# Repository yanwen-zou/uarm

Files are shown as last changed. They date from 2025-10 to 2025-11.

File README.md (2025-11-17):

# 🤖 Lerobot Anything








<p align="center">
  xArm Demo
  Dobot Demo
  ARX Demo
</p>

---

> **🚀 Bringing Leader-Follower teleoperation system to every real robot and robot arm -- Cheaper, Smoother, Plug-and-Play**
> **💵 Starts from $60 cost!! Then controls any robot arm system!!**

*Built upon the giants: [LeRobot](https://github.com/huggingface/lerobot), [SO-100/SO-101](https://github.com/TheRobotStudio/SO-ARM100), [XLeRobot](https://github.com/Vector-Wangel/XLeRobot#), [Gello](https://github.com/wuphilipp/gello_mechanical/tree/main)*

# 📰 News
- 2025-11-10: **Global version** based on Feetech STS3215 servo is launched! Chech [here](https://docs.google.com/document/d/1dUN4sJhYx_iuS_rFvj-YpyX4Y7nneRDTKJxCQ7PTXpY/edit?usp=sharing).
- 2025-11-1: We add support for SO-100 and XLeRobot Teleoperation! Check [here](github.com/MINT-SJTU/LeRobot-Anything-U-Arm/tree/main/src/uarm/scripts/Follower_Arm/LeRobot).
- 2025-09-10: STEP files of 3 configs are uploaded.
- 2025-09-08: Hardware Assembly Video Uploaded! We also open-sourced 5 datasets collected by UArm with XArm6 at [our huggingface page](https://huggingface.co/MINT-SJTU)
- 2025-08-15: **LeRobot Anything UArm 0.1.0** hardware setup, the 1st version fully capable for three major robot arm configurations, starts from 60$.

---

# 📋 Table of Contents

- [Overview](#-overview)
- [✨ Features](#-features)
- [💵 Total Cost](#-total-cost-)
- [🤖 Supported Robots (find your robot in the list!)](#-supported-robots)
- [🚀 Quick Start](#-quick-start)
- [🔮 Roadmap](#-roadmap)
- [🤝 Contributing](#-contributing)
- [🔧 Tired of DIY? Order Now](#-Order-Link)
---

## 🎯 Overview

LeRobot Anything is a **low-cost, universal, leader-follower teleoperation system** for any commercial robot arms through 3 hardware configurations. Designed for researchers, educators, and robotics enthusiasts, it provides a standardized interface for diverse robot platforms. This project focus on extending the Lerobot to control any real robot in both real scene and simulation. 

For detail, see our technical report [here](https://arxiv.org/abs/2509.02437).

### 🎯 Target Environment (Docker coming soon)

- **OS**: Ubuntu 20.04
- **ROS**: Noetic
- **Simulation**: SAPIEN integration (Built upon [ManiSkill](https://github.com/haosulab/ManiSkill))

---

## ✨ Features

| Feature | Description |
| --- | --- |
| 🔄**Universal Compatibility** | Four teleop configurations covering **most (95%) commercial robot arms** |
| 📡**ROS Integration** | Native ROS1 support with `/servo_angles` topic publishing |
| 🎮**Real-time Control** | Low-latency joint-space control |
| 🔌**Plug & Play** | Easy follower-arm integration with provided examples |
| 🛠️**Extensible** | Simple API for adding new robot support |
| 💰**Cost-effective** | Ultra low-cost hardware solution |
| 🎯**Optimized Hardware** | Move smoothly and flexibly |
| 💻**Simulation Test** | Support teleoperation test in simulation environment |

### 🎮 Ready-to-Use Examples

**Real Robot Examples:**

<p align="center">

| Dobot CR5 | xArm Series | ARX5 |
|---|---|---|
| Dobot CR5 Real Robot | xArm Series Real Robot | ARX5 Real Robot |

</p>

**Simulation Examples:**

<p align="center">

| SO100 | ARX-X5 | XLeRobot |
|---|---|---|
| SO100 Simulation | ARX-X5 Simulation | XLeRobot Simulation |

| xArm Series | Franka Panda | Piper |
|---|---|---|
| xArm Series Simulation | Franka Panda Simulation | Piper Simulation |

</p> 

## 💵 Total Cost 💵

> [!NOTE]
> Cost excludes 3D printing, tools, shipping, and taxes.

| Price | US | EU | CN |
| --- | --- | --- | --- |
| **Basic** (use your laptop) | **~$60** | **~€60** | **~¥360** |
| ↑ Servos | +$60 | +€60 | +¥405 |

---

## 🤖 Supported Robots (find your robot in the list!)

| Configuration | Compatible Robot Arms | Status |
| --- | --- | --- |
| [**Config 1**](https://github.com/MINT-SJTU/LeRobot-Anything-U-Arm/tree/main/mechanical/Config1_STL) | Xarm6, Fanuc LR Mate 200iD, Trossen ALOHA, Agile PiPER, Realman RM65B, KUKA LBR iiSY Cobot | ✅ Ready |
| [**Config 2**](https://github.com/MINT-SJTU/LeRobot-Anything-U-Arm/tree/main/mechanical/Config2_STL) | Dobot CR5, UR5, ARX R5*, AUBO i5, JAKA Zu7 | ✅ Ready |
| [**Config 3**](https://github.com/MINT-SJTU/LeRobot-Anything-U-Arm/tree/main/mechanical/Config3_STL) | Franka FR3, Franka Emika Panda, Flexiv Rizon, Realman RM75B , Xarm7 | ✅ Ready |

> 💡 **This is only part of our supported robots! For more robots, you can compare their mechanical configuration with each U-Arm to confirm which one fits your need (in most cases it will).

---

## 🚀 Quick Start

> [!NOTE]
> If you are totally new to programming, please spend at least a day to get yourself familiar with basic Python, Ubuntu and GitHub (with the help of Google and AI). At least you should know how to set up Ubuntu system, git clone, pip install, use interpreters (VS Code, Cursor, PyCharm, etc.) and directly run commands in the terminals.

1. 💵 **Buy your parts**: [Bill of Materials](https://docs.google.com/document/d/1TjhJOeJXsD5kmoYF-kuWfPju6WSUeSnivJiU7TH4vWs/edit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)
2. 🖨️ **Print your stuff**: [3D printing](https://github.com/MINT-SJTU/Lerobot-Anything-U-arm/tree/main/mechanical)
3. 🔨 **Assemble**! [Assembly Guide](https://www.youtube.com/watch?v=-gpYuN2LlVs)
4. 💻 **Software Env Set up & Real-world Teleop**: [Get your robot moving!](https://github.com/MINT-SJTU/Lerobot-Anything-Uarm/blob/main/howtoplay.md)
5. 🎮 **Simulation**: [Try it out in SAPIEN!](https://github.com/MINT-SJTU/Lerobot-Anything-U-arm/blob/main/src/simulation/README.md)

For detailed hardware guide, check  [Hardware Guide](https://docs.google.com/document/d/1TjhJOeJXsD5kmoYF-kuWfPju6WSUeSnivJiU7TH4vWs/edit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)

---

## 🔮 Roadmap

### 🎯 TO-DO List

- [X] **SAPIEN Simulation Environment**: Install and Play!

  - Virtual teleop setup mirroring physical hardware
  - Rapid prototyping and testing capabilities
  - Integration with existing SAPIEN workflows
- [ ] **ROS2 Support**
- [ ] **Docker Image**
- [ ] **Humanoid System: Config4**

---

## 🤝 Contributing

We welcome contributions! Here's how you can help:

### 💡 Feature Requests

### 🔧 Code Contributions

### 🤖 Adding New Robot Support

---

## ❓ FAQ

### 1. Is this project compatible with my XXX robot arm?
**A:** Please first refer to the **Supported Robots** section above, where part of compatible arms are listed along with corresponding config.  Note that this project aims to provide a **universal teleoperation framework** and example control code. Here, “compatibility” means that the operator can intuitively control the corresponding follower arm on hardware side by using UArm.  
This is independent of different brands’ software APIs — it only depends on the **joint topology** of the robot.  To find your robot’s joint topology, check [Hardware Guide](https://docs.google.com/document/d/1TjhJOeJXsD5kmoYF-kuWfPju6WSUeSnivJiU7TH4vWs/edit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).

---

### 2. How can I develop based on my own follower arm?
**A:** Start by reading [`LeRobot-Anything-U-Arm/src/uarm/scripts/Uarm_teleop/servo_reader`](https://github.com/MINT-SJTU/LeRobot-Anything-U-Arm/blob/main/src/uarm/scripts/Uarm_teleop/servo_reader.py).  
This script reads all UArm joint angles and is wrapped as a ROS node.  
You need to write a **subscriber** based on your follower arm’s API that receives joint commands from the `'/servo_angles'` topic and sends them to your arm.  [`Dobot Controller`](https://github.com/MINT-SJTU/LeRobot-Anything-U-Arm/blob/main/src/uarm/scripts/Follower_Arm/Dobot/servo2Dobot.py) is a simple example.

If you prefer not to use ROS communication, you can directly read the UArm’s servo command data and send them to your follower arm.  
See this [`ARX example`](https://github.com/MINT-SJTU/LeRobot-Anything-U-Arm/blob/main/src/uarm/scripts/Follower_Arm/ARX/arx_teleop.py) for reference.

## 🔧 Order Link
If you are tired of DIY, buy it on [JD 京东链接](https://item.jd.com/10170154240149.html) or contact business@evomind-tech.com for purchase.
Please note your Robotic Arm brand and model. 下单/咨询请注明使用的机械臂具体品牌型号。如有技术问题需要解答，请通过下方二维码进入社区群里咨询，京东上不便于回答讨论详细技术问题。

## 👥 Contributors

- **Yanwen Zou** - Hardware&Software System Design
- **Zhaoye Zhou** - Hareware Assemble and Adjustment
- **Chenyang Shi** - SAPIEN and website setup
- **Zewei Ye** - LeRobot adaptation and real-world Experiment
- **Yanhan Sun** - Feetech Version Design
- **Jiaqi Lu** - Real-world Experiment
- **Jie Yi** - Real-world Experiment
- **Nuobei Zhu** - Hardware and Production Optimization 
- **Siyuan Wang, Lixing Zou** - Hardware Assemble
- **Junda Huang** - Idea Discussion and website setup
- **Gaotian Wang** - Idea Discussion

This project builds upon the excellent work of:

- [LeRobot](https://github.com/huggingface/lerobot) - The foundation for robot learning
- [SO-100/SO-101](https://github.com/TheRobotStudio/SO-ARM100) - Hardware inspiration
- [XLeRobot](https://github.com/Vector-Wangel/XLeRobot) - Extended robot support
- [Gello](https://github.com/wuphilipp/gello_mechanical/tree/main) - Hardware inspiration

Thanks to all the talented contributors behind these detailed and professional projects! You are also welcomed to join our WeChat Community for discussion and questions:
<div align="center">
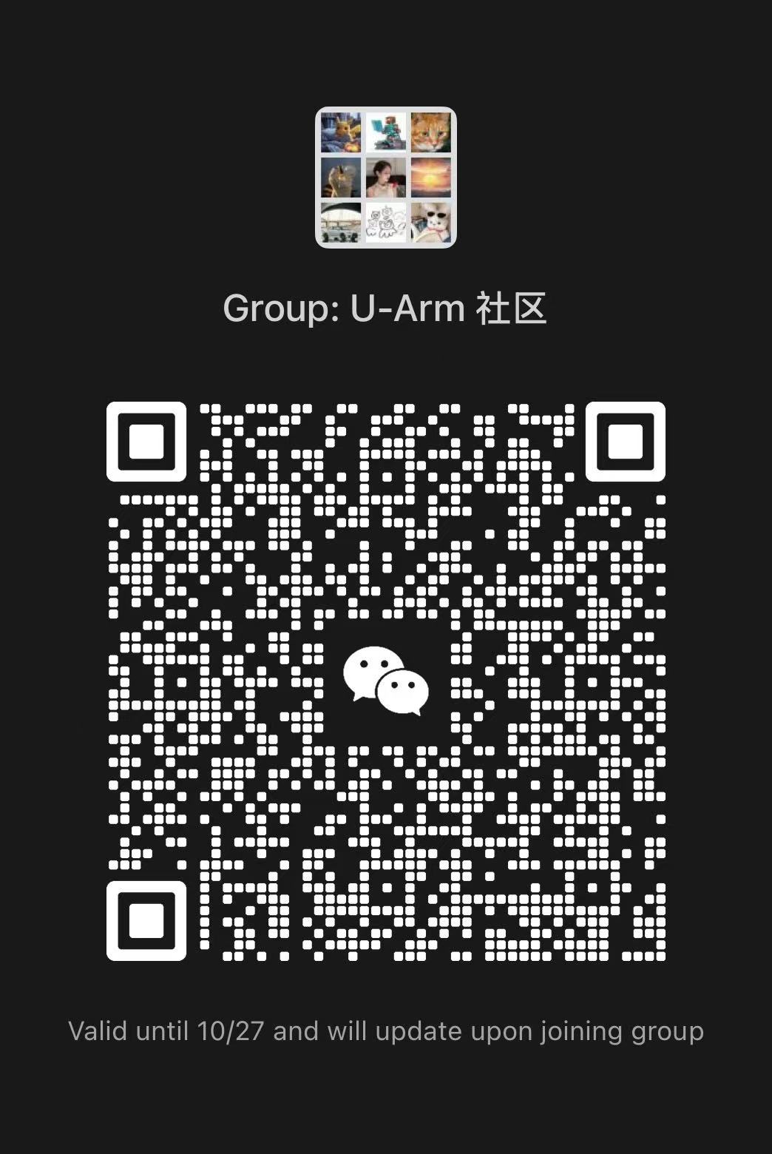
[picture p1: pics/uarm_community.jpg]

</div>
---

<div align="center">

**Made with ❤️ for the robotics community**




</div>

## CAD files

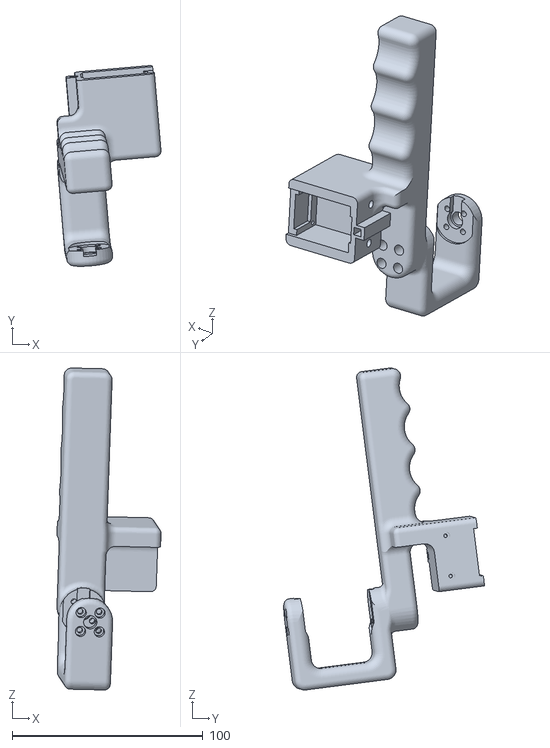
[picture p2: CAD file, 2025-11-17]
mechanical/Feetech_servo/Config1 - STL/Config1_STL/config1 - link6-1.STL
54.5 x 105.2 x 168.7

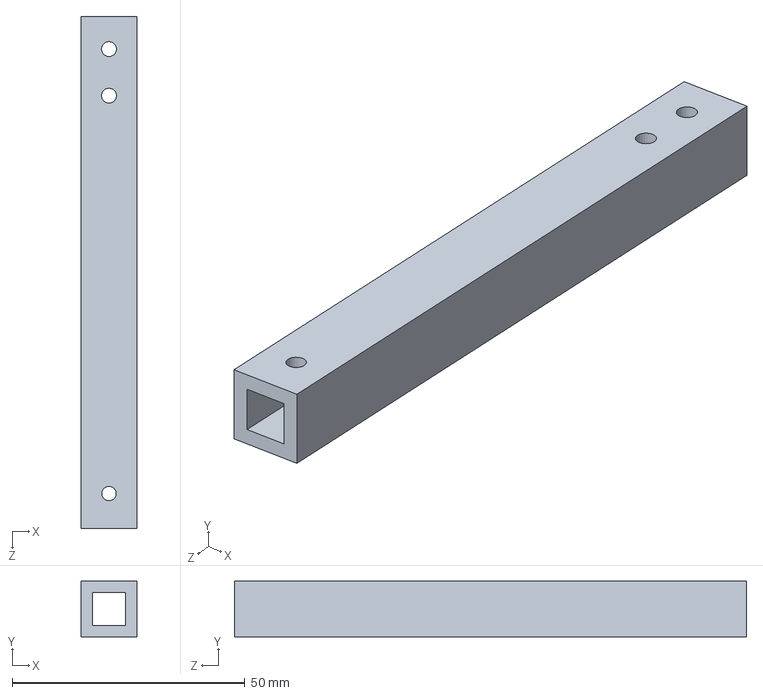
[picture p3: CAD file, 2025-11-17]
mechanical/Feetech_servo/Config1 - STL/sitter.SLDPRT
12.0 x 12.0 x 110.0 mm

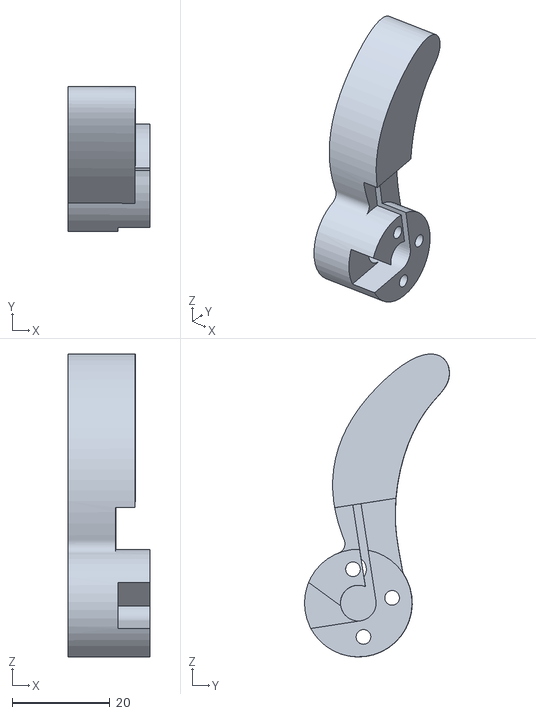
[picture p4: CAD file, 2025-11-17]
mechanical/Feetech_servo/Config2 - STL/Config2_STL/config2 - trigger_short-1.STL
16.8 x 29.6 x 61.9

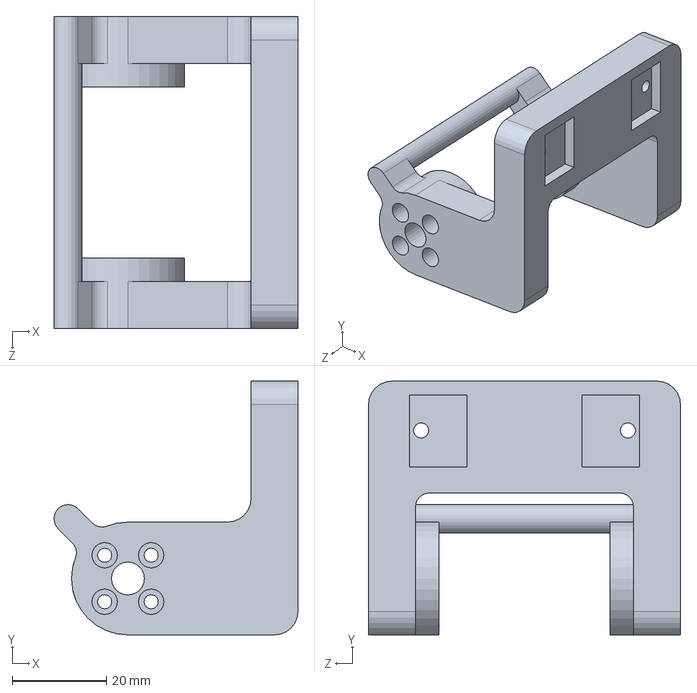
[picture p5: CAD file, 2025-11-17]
mechanical/Feetech_servo/Config2 - STL/link3_1.SLDPRT
51.9 x 54.0 x 66.4 mm

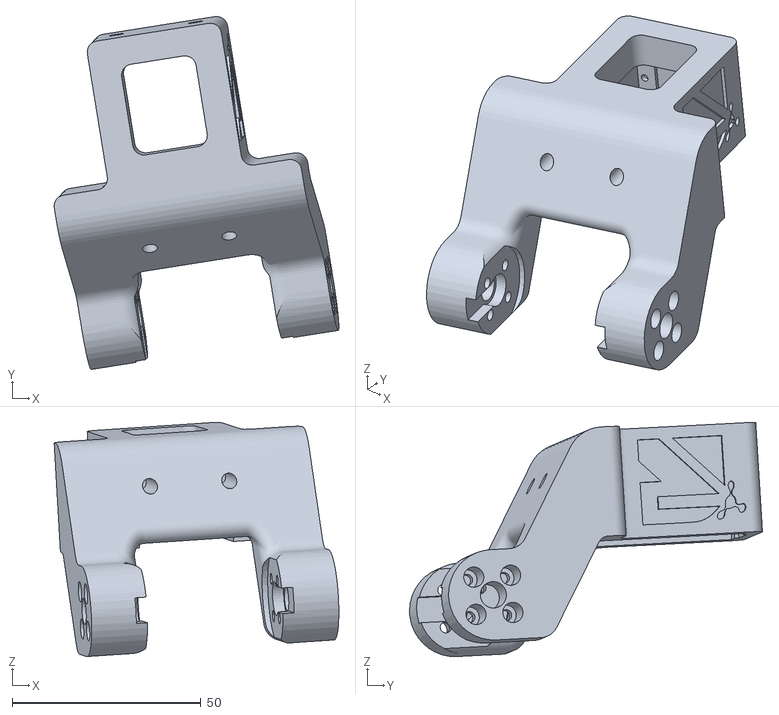
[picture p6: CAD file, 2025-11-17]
mechanical/Feetech_servo/Config3 - STL/Config3_STL/config3 - link6-1.STL
75.4 x 93.5 x 62.0

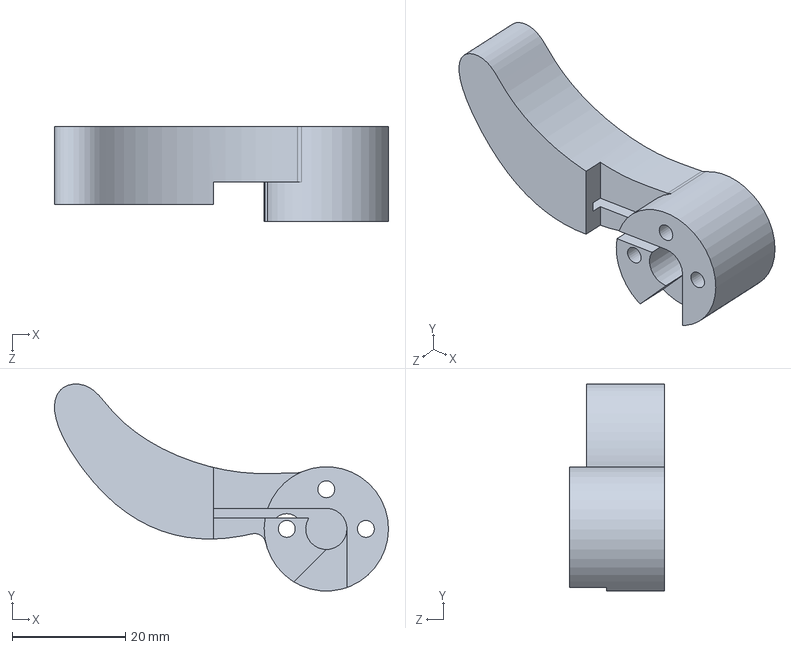
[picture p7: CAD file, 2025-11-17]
mechanical/Feetech_servo/Config3 - STL/trigger_short.SLDPRT
59.1 x 36.6 x 16.8 mm

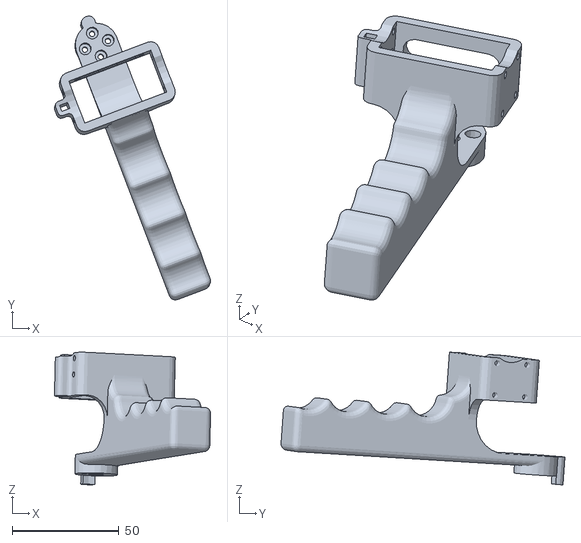
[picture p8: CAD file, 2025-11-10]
mechanical/Zhonglin_servo/Config1_STL/Config1 - trigger_handle-1.STL
73.0 x 132.8 x 62.0

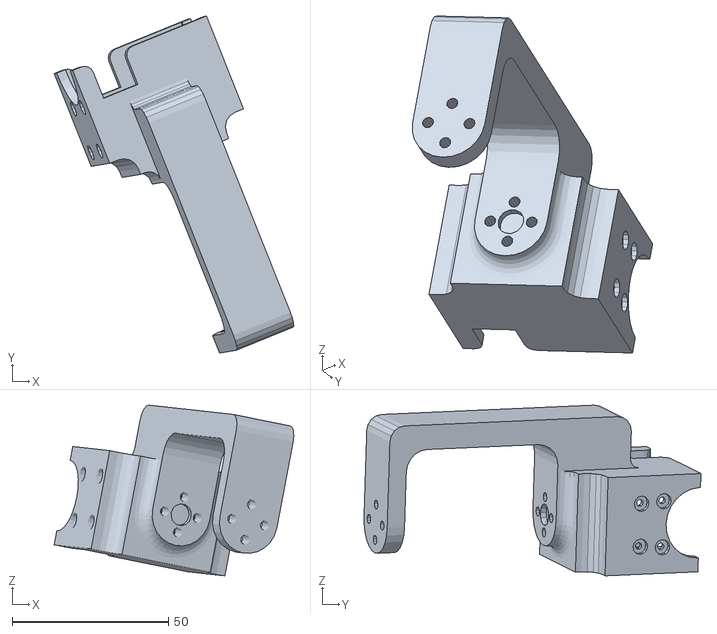
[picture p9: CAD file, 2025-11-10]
mechanical/Zhonglin_servo/Config2_STL/Config2 - link_1-2.STL
76.7 x 107.8 x 54.6

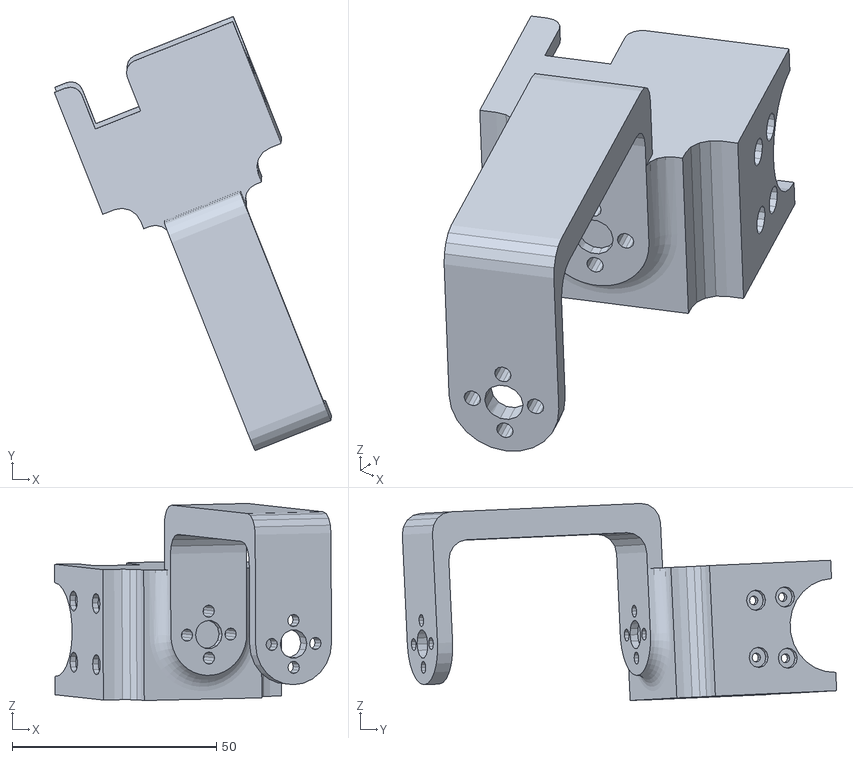
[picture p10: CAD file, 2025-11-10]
mechanical/Zhonglin_servo/Config3_STL/Config3 - link_1-1.STL
67.9 x 106.4 x 48.3

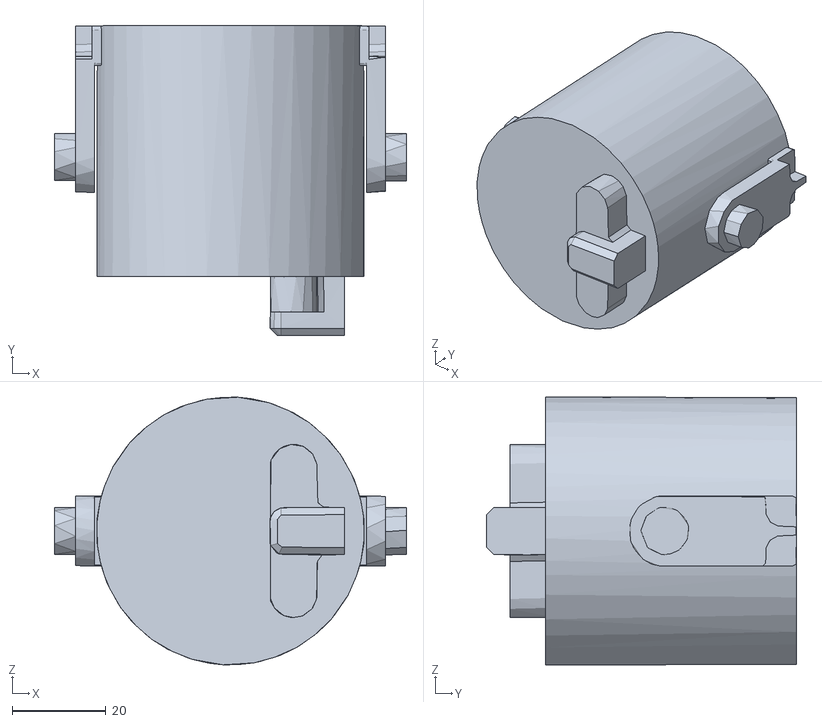
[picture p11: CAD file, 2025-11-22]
src/simulation/mani_skill/assets/robots/openarm_bi/meshes/arm/v10/collision/link6_symp.stl
75.0 x 66.0 x 57.0

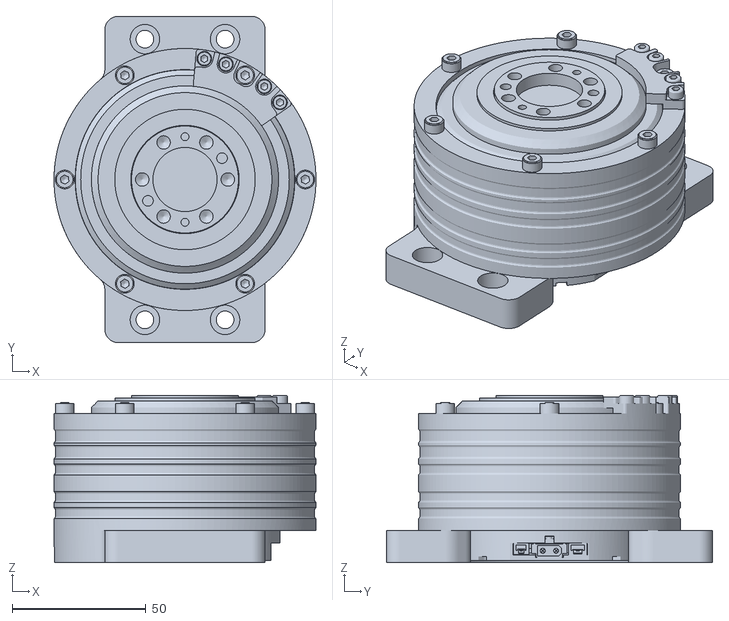
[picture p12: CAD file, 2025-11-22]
src/simulation/mani_skill/assets/robots/openarm_bi/meshes/arm/v10/visual/link0.stl
98.0 x 122.0 x 62.5

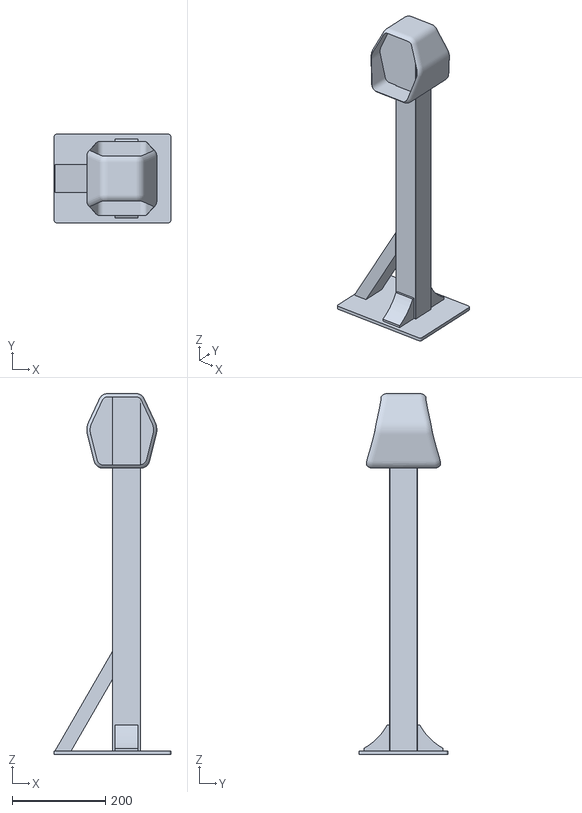
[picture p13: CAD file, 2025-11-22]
src/simulation/mani_skill/assets/robots/openarm_bi/meshes/body/v10/collision/body_link0_symp.stl
250.0 x 190.0 x 773.0

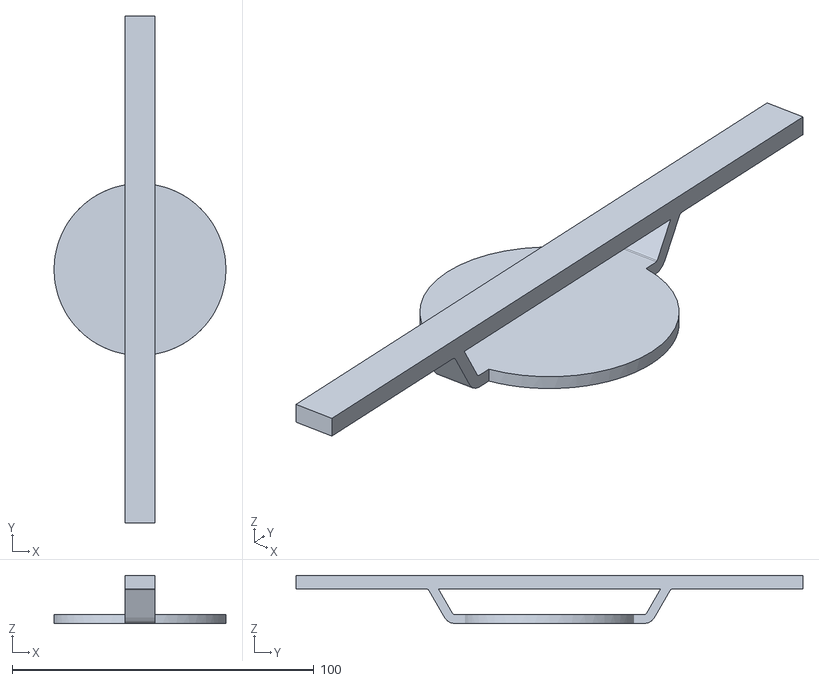
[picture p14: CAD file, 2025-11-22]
src/simulation/mani_skill/assets/robots/openarm_bi/meshes/ee/openarm_hand/collision/hand.stl
57.0 x 168.1 x 16.0

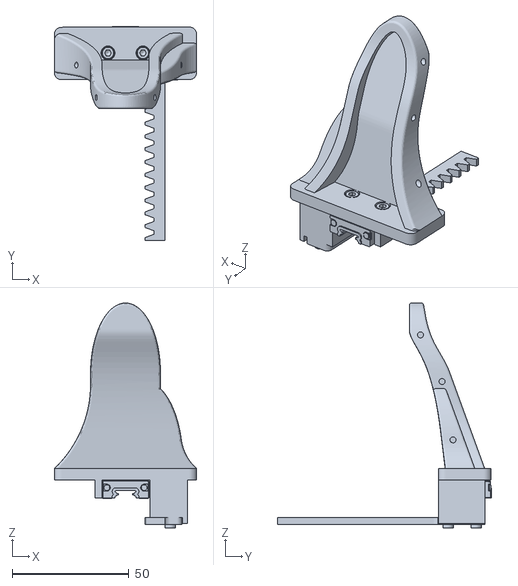
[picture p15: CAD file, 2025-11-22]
src/simulation/mani_skill/assets/robots/openarm_bi/meshes/ee/openarm_hand/visual/finger.stl
61.0 x 92.0 x 96.5

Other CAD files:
mechanical/Feetech_servo/Config1 - STL/base0.SLDPRT
mechanical/Feetech_servo/Config1 - STL/Config1_STL/config1 - sitter-1.STL
mechanical/Feetech_servo/Config2 - STL/Config2_STL/config2 - link2-1.STL
mechanical/Feetech_servo/Config2 - STL/link6.SLDPRT
mechanical/Feetech_servo/Config1 - STL/Config1_STL/config1 - base-1.STL
mechanical/Feetech_servo/Config1 - STL/Config1_STL/config1 - link1-1.STL
mechanical/Feetech_servo/Config1 - STL/Config1_STL/config1 - link2-1.STL
mechanical/Feetech_servo/Config1 - STL/Config1_STL/config1 - link3_1-1.STL
mechanical/Feetech_servo/Config1 - STL/Config1_STL/config1 - link3_2-1.STL
mechanical/Feetech_servo/Config1 - STL/Config1_STL/config1 - link4-1.STL
mechanical/Feetech_servo/Config1 - STL/Config1_STL/config1 - link5-1.STL
mechanical/Feetech_servo/Config1 - STL/Config1_STL/config1 - sitter-2.STL
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

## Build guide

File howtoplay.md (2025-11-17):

# 🔧 System Setup

## Prerequisites

- **Ubuntu 20.04**
- [**ROS Noetic**](https://wiki.ros.org/noetic/Installation/Ubuntu)
- **Python 3.9+**

---

## Step-by-Step Setup

1. **Install Python Dependencies**

   ```sh
   # install both ros1 and simulation requirements
   pip install -r overall_requirements.txt 
   ```
   
   If your system doesn't support ROS1, you can install the dependencies without ROS1 with the following command which supports simulation teleoperation and check [this note](https://github.com/MINT-SJTU/Lerobot-Anything-U-arm/blob/main/src/simulation/README.md) . 
   ```sh
   pip install -r requirements.txt
   ```

3. **Build Catkin Workspace**

   ```sh
   catkin_make
   source devel/setup.bash
   ```

4. **Verify Installation**

   ```sh
   # Test if ROS can find the package
   rospack find uarm
   ```

---

# 🤖 Plug-and-Play with Real Robot with ROS1
> Zhonglin servo version
## 1. Start ROS Core

Open a terminal and run:

```sh
roscore
```

## 2. Verify Teleop Arm Output

In a new terminal, check servo readings:

```sh
rosrun uarm servo_zero.py
```

This will display real-time angles from all servos. You should check whether `SERIAL_PORT` is available on your device and modify the variable if necessary. 

## 3. Publish Teleop Data

Still in the second terminal, start the teleop publisher:

```sh
rosrun uarm servo_reader.py
```

Your teleop arm now publishes to the `/servo_angles` topic.

## 4. Control the Follower Arm

Choose your robot and run the corresponding script:

- **For Dobot CR5:**
  ```sh
  rosrun uarm scripts/Follower_Arm/Dobot/servo2Dobot.py
  ```

- **For xArm:**
  ```sh
  rosrun uarm scripts/Follower_Arm/xarm/servo2xarm.py
  ```

---

> Feetech servo version (Global Version)
## 1. Start ROS Core

Open a terminal and run:

```sh
roscore
```

## 2. Verify Teleop Arm Output

In a new terminal, check servo readings:

```sh
rosrun uarm feetech_servo_zero.py
```

This will display real-time angles from all servos. You should check whether `SERIAL_PORT` is available on your device and modify the variable if necessary. You may find all servos' angles are `2047` since servo's position is set as `2047` (0~4095 for $360^\circ$) when this code starts running.

## 3. Publish Teleop Data

Still in the second terminal, start the teleop publisher:

```sh
rosrun uarm feetech_servo_reader.py
```

Servo's position is set again as `2047` when this code starts running . **Please return UARM to initial position before starting this script.** Your teleop arm now publishes to the `/servo_angles` topic.

## 4. Control the Follower Arm

Choose your robot and run the corresponding script:

- **For Dobot CR5:**
  ```sh
  rosrun uarm scripts/Follower_Arm/Dobot/servo2Dobot.py
  ```

- **For xArm:**
  ```sh
  rosrun uarm scripts/Follower_Arm/xarm/servo2xarm.py
  ```
---

# 🖥️ Try It Out in Simulation

If you do not have robot hardware, you can try teleoperation in simulation.  
See detailed guidance [here](https://github.com/MINT-SJTU/Lerobot-Anything-U-arm/blob/feat/simulation/src/simulation/README.md).

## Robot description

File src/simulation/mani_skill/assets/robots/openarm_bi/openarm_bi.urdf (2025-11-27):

<?xml version="1.0" ?>
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
<robot name="openarm">
  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
  <link name="world"/>
  <joint name="openarm_body_world_joint" type="fixed">
    <parent link="world"/>
    <child link="openarm_body_link0"/>
    <origin rpy="0 0 0" xyz="0 0 0"/>
  </joint>
  <link name="openarm_body_link0">
    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
    <inertial>
      <origin rpy="0.0 0.0 0.0" xyz="0.0 0.0 0.0"/>
      <mass value="13.89"/>
      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
    </inertial>
  </link>
  <joint name="openarm_left_openarm_body_link0_joint" type="fixed">
    <parent link="openarm_body_link0"/>
    <child link="openarm_left_link0"/>
    <origin rpy="-1.5708 0 0" xyz="0.0 0.031 0.698"/>
  </joint>
  <link name="openarm_left_link0">
    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
    <inertial>
      <origin rpy="0.0 0.0 0.0" xyz="-0.0009483362816297526 -0.0001580207020448382 0.03076860287587199"/>
      <mass value="1.1432284943239561"/>
      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
    </inertial>
  </link>
  <link name="openarm_left_link1">
    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
    <inertial>
      <origin rpy="0.0 0.0 0.0" xyz="0.0011467657911800769 -3.319987657026362e-05 0.05395284380736254"/>
      <mass value="1.1416684646202298"/>
      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
    </inertial>
  </link>
  <joint name="openarm_left_joint1" type="revolute">
    <origin rpy="0 0 0" xyz="0.0 0.0 0.0625"/>
    <parent link="openarm_left_link0"/>
    <child link="openarm_left_link1"/>
    <axis xyz="0 0 1"/>
    <limit effort="40" lower="-3.490659" upper="1.3962629999999998" velocity="16.754666"/>
  </joint>
  <link name="openarm_left_link2">
    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
    <inertial>
      <origin rpy="0.0 0.0 0.0" xyz="0.00839629182351943 2.0145102027597523e-08 0.03256649300522363"/>
      <mass value="0.2775092746011571"/>
      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
    </inertial>
  </link>
  <joint name="openarm_left_joint2" type="revolute">
    <origin rpy="-1.57079632679 0 0" xyz="-0.0301 0.0 0.06"/>
    <parent link="openarm_left_link1"/>
    <child link="openarm_left_link2"/>
    <axis xyz="-1 0 0"/>
    <limit effort="40" lower="-3.3161253267948965" upper="0.17453267320510335" velocity="16.754666"/>
  </joint>
  <link name="openarm_left_link3">
    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
    <inertial>
      <origin rpy="0.0 0.0 0.0" xyz="-0.002104752099628911 -0.0005549085042607548 0.09047470545721961"/>
      <mass value="1.073863338202347"/>
      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
    </inertial>
  </link>
  <joint name="openarm_left_joint3" type="revolute">
    <origin rpy="0 0 0" xyz="0.0301 0.0 0.06625"/>
    <parent link="openarm_left_link2"/>
    <child link="openarm_left_link3"/>
    <axis xyz="0 0 1"/>
    <limit effort="27" lower="-1.570796" upper="1.570796" velocity="5.445426"/>
  </joint>
  <link name="openarm_left_link4">
    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
    <inertial>
      <origin rpy="0.0 0.0 0.0" xyz="-0.0029006831074562967 -0.03030575826634669 0.06339637422196209"/>
      <mass value="0.6348534566833373"/>
      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
    </inertial>
  </link>
  <joint name="openarm_left_joint4" type="revolute">
    <origin rpy="0 0 0" xyz="-0.0 0.0315 0.15375"/>
    <parent link="openarm_left_link3"/>
    <child link="openarm_left_link4"/>
    <axis xyz="0 1 0"/>
    <limit effort="27" lower="0.0" upper="2.443461" velocity="5.445426"/>
  </joint>
  <link name="openarm_left_link5">
    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
    <inertial>
      <origin rpy="0.0 0.0 0.0" xyz="-0.003049665024221911 -0.0008866902457326625 0.043079803024980934"/>
      <mass value="0.6156588026168502"/>
      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
    </inertial>
  </link>
  <joint name="openarm_left_joint5" type="revolute">
    <origin rpy="0 0 0" xyz="0.0 -0.0315 0.0955"/>
    <parent link="openarm_left_link4"/>
    <child link="openarm_left_link5"/>
    <axis xyz="0 0 1"/>
    <limit effort="7" lower="-1.570796" upper="1.570796" velocity="20.943946"/>
  </joint>
  <link name="openarm_left_link6">
    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
    <inertial>
      <origin rpy="0.0 0.0 0.0" xyz="-0.037136587005447405 -0.00033230528343419053 -9.498374522309838e-05"/>
      <mass value="0.475202773187987"/>
      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
    </inertial>
  </link>
  <joint name="openarm_left_joint6" type="revolute">
    <origin rpy="0 0 0" xyz="0.0375 0.0 0.1205"/>
    <parent link="openarm_left_link5"/>
    <child link="openarm_left_link6"/>
    <axis xyz="1 0 0"/>
    <limit effort="7" lower="-0.785398" upper="0.785398" velocity="20.943946"/>
  </joint>
  <link name="openarm_left_link7">
    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
    <inertial>
      <origin rpy="0.0 0.0 0.0" xyz="6.875510271106056e-05 -0.01266175250761268 0.06951945409987448"/>
      <mass value="0.4659771327380578"/>
      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
    </inertial>
  </link>
  <joint name="openarm_left_joint7" type="revolute">
    <origin rpy="0 0 0" xyz="-0.0375 0.0 0.0"/>
    <parent link="openarm_left_link6"/>
    <child link="openarm_left_link7"/>
    <axis xyz="0 -1 0"/>
    <limit effort="7" lower="-1.570796" upper="1.570796" velocity="20.943946"/>
  </joint>
  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
  <joint name="openarm_right_openarm_body_link0_joint" type="fixed">
    <parent link="openarm_body_link0"/>
    <child link="openarm_right_link0"/>
    <origin rpy="1.5708 0 0" xyz="0.0 -0.031 0.698"/>
  </joint>
  <link name="openarm_right_link0">
    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
    <inertial>
      <origin rpy="0.0 0.0 0.0" xyz="-0.0009483362816297526 0.0001580207020448382 0.03076860287587199"/>
      <mass value="1.1432284943239561"/>
      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
    </inertial>
  </link>
  <link name="openarm_right_link1">
    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
    <inertial>
      <origin rpy="0.0 0.0 0.0" xyz="0.0011467657911800769 3.319987657026362e-05 0.05395284380736254"/>
      <mass value="1.1416684646202298"/>
      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
    </inertial>
  </link>
  <joint name="openarm_right_joint1" type="revolute">
    <origin rpy="0 0 0" xyz="0.0 0.0 0.0625"/>
    <parent link="openarm_right_link0"/>
    <child link="openarm_right_link1"/>
    <axis xyz="0 0 1"/>
    <limit effort="40" lower="-1.396263" upper="3.490659" velocity="16.754666"/>
  </joint>
  <link name="openarm_right_link2">
    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
    <inertial>
      <origin rpy="0.0 0.0 0.0" xyz="0.00839629182351943 -2.0145102027597523e-08 0.03256649300522363"/>
      <mass value="0.2775092746011571"/>
      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
    </inertial>
  </link>
  <joint name="openarm_right_joint2" type="revolute">
    <origin rpy="1.57079632679 0 0" xyz="-0.0301 0.0 0.06"/>
    <parent link="openarm_right_link1"/>
    <child link="openarm_right_link2"/>
    <axis xyz="-1 0 0"/>
    <limit effort="40" lower="-0.17453267320510335" upper="3.3161253267948965" velocity="16.754666"/>
  </joint>
  <link name="openarm_right_link3">
    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
    <inertial>
      <origin rpy="0.0 0.0 0.0" xyz="-0.002104752099628911 0.0005549085042607548 0.09047470545721961"/>
      <mass value="1.073863338202347"/>
      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
    </inertial>
  </link>
  <joint name="openarm_right_joint3" type="revolute">
    <origin rpy="0 0 0" xyz="0.0301 0.0 0.06625"/>
    <parent link="openarm_right_link2"/>
    <child link="openarm_right_link3"/>
    <axis xyz="0 0 1"/>
    <limit effort="27" lower="-1.570796" upper="1.570796" velocity="5.445426"/>
  </joint>
  <link name="openarm_right_link4">
    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
    <inertial>
      <origin rpy="0.0 0.0 0.0" xyz="-0.0029006831074562967 -0.03030575826634669 0.06339637422196209"/>
      <mass value="0.6348534566833373"/>
      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
    </inertial>
  </link>
  <joint name="openarm_right_joint4" type="revolute">
    <origin rpy="0 0 0" xyz="-0.0 0.0315 0.15375"/>
    <parent link="openarm_right_link3"/>
    <child link="openarm_right_link4"/>
    <axis xyz="0 1 0"/>
    <limit effort="27" lower="0.0" upper="2.443461" velocity="5.445426"/>
  </joint>
  <link name="openarm_right_link5">
    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
    <inertial>
      <origin rpy="0.0 0.0 0.0" xyz="-0.003049665024221911 0.0008866902457326625 0.043079803024980934"/>
      <mass value="0.6156588026168502"/>
      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
    </inertial>
  </link>
  <joint name="openarm_right_joint5" type="revolute">
    <origin rpy="0 0 0" xyz="0.0 -0.0315 0.0955"/>
    <parent link="openarm_right_link4"/>
    <child link="openarm_right_link5"/>
    <axis xyz="0 0 1"/>
    <limit effort="7" lower="-1.570796" upper="1.570796" velocity="20.943946"/>
  </joint>
  <link name="openarm_right_link6">
    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
    <inertial>
      <origin rpy="0.0 0.0 0.0" xyz="-0.037136587005447405 0.00033230528343419053 -9.498374522309838e-05"/>
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

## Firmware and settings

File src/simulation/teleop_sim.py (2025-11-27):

import serial
import time 
import numpy as np
import re
import gymnasium as gym
import mani_skill.envs  # Must import to register all env/agent
from threading import Event, Thread, Lock
from queue import Queue, Empty
import torch
import sapien
import argparse
from mani_skill.utils import sapien_utils


class ServoTeleoperatorSim: 
    """Robot arm teleoperation simulation system
    
    Supports reading servo angles through serial port and mapping to different types of robot arm simulation environments.
    Supported robot arm types: arx-x5, so100, xarm6_robotiq, panda, x_fetch, unitree_h1
    """
    
    def __init__(
        self,
        scene: str,
        robot_uids: str,
        serial_port: str = "/dev/ttyUSB0",
        serial_port2: str = "/dev/ttyUSB1",
        shader: str | None = "default",
        main_thread_render: bool = True,
    ):
        """Initialize teleoperation system
        
        Args:
            scene: Simulation scene name
            robot_uids: Robot arm type identifier
            serial_port: Serial port device path
            serial_port2: Second serial port (used for dual-arm setups)
            shader: Rendering shader pack. Use "default" (stable) instead of "rt-fast" if the GPU
                cannot run the ray-tracing pipeline to avoid viewer crashes.
            main_thread_render: If True, run step/render on the main thread to avoid driver
                crashes caused by off-main rendering on some platforms.
        """
        # Serial port configuration
        self.SERIAL_PORT = serial_port
        self.SERIAL_PORT2 = serial_port2 if robot_uids == "openarm_bi" else None
        self.BAUDRATE = 115200
        self.ser_primary = serial.Serial(self.SERIAL_PORT, self.BAUDRATE, timeout=0.01)
        self.ser_secondary = (
            serial.Serial(self.SERIAL_PORT2, self.BAUDRATE, timeout=0.01)
            if self.SERIAL_PORT2
            else None
        )

        # System configuration
        self.scene = scene
        self.robot_uids = robot_uids
        self.gripper_range = 0.48
        # Reserve storage for incoming servo angles (8 DOF by default; 16 for dual-arm OpenArm)
        self.main_thread_render = main_thread_render
        if robot_uids == "openarm_bi":
            self.zero_angles = [0.0] * 16
            self.sim_init_angles = [0.0] * 16
        else:
            self.zero_angles = [0.0] * 8  # Initial calibration angles for servos
            self.sim_init_angles = [0.0] * 8  # Simulation initial angles
        self.stop_event = Event()
        self.rate = 50.0  # Control frequency
        
        # Initialize servos and calibrate zero position
        self._init_servos()

        # Thread-safe data exchange queue
        self.arm_pos_queue: "Queue[list]" = Queue(maxsize=1)

        # Select control mode based on robot type
        if robot_uids == "x_fetch": 
            self.control_mode = "pd_joint_pos_dual_arm"
        elif robot_uids == "unitree_h1":
            self.control_mode = "pd_joint_pos"
        else: 
            self.control_mode = "pd_joint_pos"

        render_kwargs = {}
        if shader:
            render_kwargs.update(
                sensor_configs=dict(shader_pack=shader),
                human_render_camera_configs=dict(shader_pack=shader),
                viewer_camera_configs=dict(shader_pack=shader),
            )

        # Create simulation environment
        self.env = gym.make(
            scene,
            robot_uids=robot_uids,
            render_mode="human",
            control_mode=self.control_mode,
            sim_config=dict(
                default_materials_config=dict(
                    static_friction=10.0,  # Static friction
                    dynamic_friction=10.0, # Dynamic friction
                    restitution=0.0       # Restitution coefficient
                )
            ),
            **render_kwargs,
        )
        obs, _ = self.env.reset(seed=0)
        print("Action space:", self.env.action_space)
        
        # Set initial standing pose for H1
        if robot_uids == "unitree_h1":
            self._setup_h1_standing_pose()

        # Create producer thread (read servo angles)
        self.produce_thread = Thread(
            target=self.angle_stream_loop, 
            args=(self.default_sender,), 
            daemon=True
        )

        # Create consumer thread (control simulation)
        self.consume_thread = None
        if not self.main_thread_render:
            self.consume_thread = Thread(
                target=self.pose_consumer_loop, 
                args=(self.teleop_sim_handler,), 
                daemon=True
            )

        self._setup_camera_pose()


    def _setup_camera_pose(self):
        agent = getattr(self.env.unwrapped, "agent", None)
        pose = sapien.Pose()
        if agent is not None:
            pose = agent.robot.get_pose()  # Returns sapien.Pose
            print(f"Robot initial position: {pose}")
        camera_pose = sapien_utils.look_at(
            [0.0, -1.5, 1.7], pose.p
        )
        camera_viewer = getattr(self.env.unwrapped, "viewer", None)
        if camera_viewer is not None:
            print(camera_pose)
            camera_pose_arr = camera_pose.raw_pose.squeeze().cpu().numpy()
            camera_position = camera_pose_arr[:3]
            camera_quaternion = camera_pose_arr[3:]
            camera_viewer.set_camera_pose(sapien.Pose(camera_position, camera_quaternion))

    def _setup_h1_standing_pose(self):
        """Set initial standing pose for H1 robot"""
        try:
            agent = getattr(self.env.unwrapped, "agent", None)
            if agent is not None:
                # Use H1 predefined standing pose
                standing_keyframe = agent.keyframes["standing"]
                
                # Check qpos dimensions
                if hasattr(standing_keyframe.qpos, '__len__') and len(standing_keyframe.qpos) >= 19:
                    agent.reset(standing_keyframe.qpos)
                    agent.robot.set_root_pose(standing_keyframe.pose)
                    print("H1 set to standing pose")
                else:
                    print("Warning: standing_keyframe.qpos dimensions incorrect, using default standing pose")
                    # Use default standing pose
                    default_standing = np.array([
                        0, 0, 0, 0, 0, 0, 0, -0.4, -0.4, 0.0, 0.0, 0.8, 0.8, 0.0, 0.0, -0.4, -0.4, 0.0, 0.0
                    ])
                    agent.reset(default_standing)
                    agent.robot.set_root_pose(standing_keyframe.pose)
                    print("H1 set to default standing pose")
        except Exception as e:
            print(f"Failed to set H1 standing pose: {e}")
    
    def _init_servos(self):
        """Initialize servos and calibrate zero position angles"""
        def _init_port(ser_obj, start_idx, count):
            self.send_command(ser_obj, "#000PVER!")
            for i in range(count):
                self.send_command(ser_obj, "#000PCSK!")
                self.send_command(ser_obj, f"#{i:03d}PULK!")
                response = self.send_command(ser_obj, f"#{i:03d}PRAD!")
                angle = self.pwm_to_angle(response.strip())
                self.zero_angles[start_idx + i] = angle if angle is not None else 0.0

        if self.robot_uids == "openarm_bi":
            _init_port(self.ser_primary, 0, 8)
            if self.ser_secondary is None:
                raise RuntimeError("openarm_bi requires a second serial port for the right arm")
            _init_port(self.ser_secondary, 8, 8)
        else:
            _init_port(self.ser_primary, 0, 7)
        print("[INFO] Servo initial angle calibration completed")

    def send_command(self, ser_obj: serial.Serial, cmd: str) -> str:
        """Send serial command and read response
        
        Args:
            ser_obj: Serial object to write to
            cmd: Command string to send
            
        Returns:
            Response string, returns empty string if no response
        """
        ser_obj.write(cmd.encode('ascii'))
        time.sleep(0.008)
        response = ser_obj.read_all()
        return response.decode('ascii', errors='ignore') if response else ""
    
    def pwm_to_angle(self, response_str: str, pwm_min: int = 500, 
                     pwm_max: int = 2500, angle_range: float = 270):
        """Convert PWM response to angle
        
        Args:
            response_str: Servo response string
            pwm_min: PWM minimum value
            pwm_max: PWM maximum value
            angle_range: Angle range (degrees)
            
        Returns:
            Angle value, returns None if parsing fails
        """
        match = re.search(r'P(\d{4})', response_str)
        if not match:
            return None
        pwm_val = int(match.group(1))
        pwm_span = pwm_max - pwm_min
        angle = (pwm_val - pwm_min) / pwm_span * angle_range
        return angle
    
    def publish_arm_pos(self, arm_pos: list):
        """Publish latest arm position to queue, overwriting old values"""
        try:
            # Clear old data from queue
            while True:
                self.arm_pos_queue.get_nowait()
        except Empty:
            pass
        try:
            # Add new data
            self.arm_pos_queue.put_nowait(list(arm_pos))
        except Exception:
            pass
    
    def get_latest_arm_pos(self, timeout: float = 0.0):
        """Get latest arm position snapshot
        
        Args:
            timeout: Timeout time, 0 means return immediately
            
        Returns:
            Latest arm position list, returns None if queue is empty
        """
        try:
            return self.arm_pos_queue.get(timeout=timeout) if timeout and timeout > 0 else self.arm_pos_queue.get_nowait()
        except Empty:
            return None
    
    def angle_to_gripper(self, angle_rad: float, pos_min: float, pos_max: float, 
                        angle_range: float = 1.5 * np.pi) -> float:
        """Map servo angle to gripper position
        
        Args:
            angle_rad: Servo angle (radians)
            pos_min: Gripper minimum position
            pos_max: Gripper maximum position
            angle_range: Servo angle range
            
        Returns:
            Gripper position value
        """
        ratio = max(0, 1 - (angle_rad / angle_range))
        position = pos_min + (pos_max - pos_min) * ratio
        return float(np.clip(position, pos_min, pos_max))

    def convert_pose_to_action(self, pose: list) -> np.ndarray: 
        """Convert servo position to simulation action based on different robot arm types
        
        Args:
            pose: Servo angle list (radians), length depends on robot (7 for single-arm, 16 for openarm_bi dual-arm)
            
        Returns:
            Corresponding robot arm action vector
        """
        action = np.array([])

        if self.robot_uids == "arx-x5":  # 6-axis robot arm + dual-finger gripper
            action = np.array(pose)
            # Handle gripper: map last dimension to gripper position
            action[-1] = self.angle_to_gripper(action[-1], 0, 0.044)
            action = np.concatenate([action, [action[-1]]])

            action[2] = -action[2]
            action[4], action[5] = -action[5], -action[4]  # Swap joints 4 and 5
        
        elif self.robot_uids == "piper":  # 6-axis robot arm + dual-finger gripper
            action = np.array(pose)
            action[-1] = self.angle_to_gripper(action[-1], 0, 0.04)

            action = np.concatenate([action, [action[-1]]])
            action[3], action[4] = action[4], -action[3]  # Swap joints 4 and 5

        elif self.robot_uids == "so100":  # 5-axis robot arm
            pose_copy = pose.copy()
            pose_copy.pop(5)  # Remove 6th dimension (so100 only has 5 axes)
            action = np.array(pose_copy)
            action[-1] = self.angle_to_gripper(action[-1], -1.1, 1.1)
            
            action[0] = -action[0]
            action[3] = -action[3]
            action[4] = -action[4]

        elif self.robot_uids == "xarm6_robotiq":  # 6-axis robot arm + Robotiq gripper
            action = np.array(pose)
            action[3], action[4] = action[4], -action[3]  # Swap joints 3 and 4
            # action[1] = -action[1]
            action[-1] = 0.81 - self.angle_to_gripper(action[-1], 0, 0.81)

        elif self.robot_uids == "panda":  # 7-axis robot arm
            pose_copy = pose.copy()
            pose_copy.insert(2, 0.0)  # Insert 0 at 3rd position (Panda's 3rd joint)
            action = np.array(pose_copy)
            # action[1] = -action[1]
            action[3] = -action[3]
            action[4], action[5] = action[5], action[4]  # Swap joints 4 and 5
            action[-1] = self.angle_to_gripper(action[-1], -1.0, 1.0)

        elif self.robot_uids == "x_fetch":  # Dual-arm robot + mobile base
            pose_copy = pose.copy()
            pose_copy.pop(5)  # Remove 6th dimension
            action = np.array(pose_copy)
            action[-1] = self.angle_to_gripper(action[-1], -1.1, 1.1)
            # Adjust joint directions
            action[0] = -action[0]
            action[1] = -action[1]
            action[3] = -action[3]
            action[4] = -action[4]
            # Build dual-arm action
            left_arm_action = action.copy()
            right_arm_action = left_arm_action.copy()
            right_arm_action[0] = -right_arm_action[0]
            right_arm_action[-2] = -right_arm_action[-2]
            # Combine: left arm joints + right arm joints + left/right grippers + base motion (0)
            zero_action = np.zeros(6)
            action = np.concatenate([
                left_arm_action[0:-1], 
                right_arm_action[0:-1], 
                [left_arm_action[-1], right_arm_action[-1]], 
                np.zeros(4) 
            ])

        elif self.robot_uids == "widowx250s":  # 6-axis robot arm + dual-finger gripper
            action = np.array(pose)
            action[-1] = self.angle_to_gripper(action[-1], 0, 0.04)
            action = np.concatenate([action, [action[-1]]])
            action[3], action[4] = action[4], -action[3] 
        
        elif self.robot_uids == "unitree_h1":  # Humanoid robot
            raw = np.array(pose, dtype=np.float32)
            action = np.zeros(19, dtype=np.float32)

            # Only modify arm joint increments (relative to current state)
            # Left arm: shoulder_pitch, shoulder_roll, shoulder_yaw, elbow
            action[5] = raw[0]  # left_shoulder_pitch increment
            action[9] = raw[1]   # left_shoulder_roll increment
            action[13] = raw[2]  # left_shoulder_yaw increment
            action[17] = raw[3]  # left_elbow increment

            # Right arm: shoulder_pitch, shoulder_roll, shoulder_yaw, elbow
            action[6] = raw[4]   # right_shoulder_pitch increment
            action[10] = raw[5]  # right_shoulder_roll increment
            action[14] = raw[6]  # right_shoulder_yaw increment
            action[18] = raw[3]  # right_elbow increment (reuse 4th servo)
        elif self.robot_uids == "openarm_bi":  # Humanoid robot
            raw = np.array(pose, dtype=np.float32)
            if raw.shape[0] != 16:
                raise ValueError(f"openarm_bi expects 16 input joints, got {raw.shape[0]}")

            # Explicit mapping to allow per-joint sign tweaks if needed
            action = np.zeros(18, dtype=np.float32)
            # Left arm 7 joints
            action[0] = raw[0]
            action[1] = raw[1]
            action[2] = raw[2]
            action[3] = raw[3]
            action[4] = raw[4]
            action[5] = raw[5]
            action[6] = raw[6]
            # Left gripper drives two finger joints
            action[7] = raw[7]
            action[8] = raw[7]
            # Right arm 7 joints
            action[9] = raw[8]
            action[10] = raw[9]
            action[11] = raw[10]
            action[12] = raw[11]
            action[13] = raw[12]
            action[14] = raw[13]
            action[15] = raw[14]
            # Right gripper drives two finger joints
            action[16] = raw[15]
            action[17] = raw[15]

        

        else: 
            raise ValueError(f"Unsupported robot arm type: {self.robot_uids}")

        return action

    def default_sender(self, arm_pos: list): 
        """Default angle sending callback (for debugging)"""
        print(f"Servo angles (degrees): {np.degrees(arm_pos)}")

    def teleop_sim_handler(self, action: np.ndarray, dwell: float = 0.01):
        """Simulation control handler function
        
        Args:
            action: Robot arm action vector
            dwell: Delay time
        """
        if self.env is None or action is None:
            return
            
        # All robot types execute actions
        self.env.step(action)
        self.env.render()
        time.sleep(dwell)
    
    def angle_stream_loop(self, on_send):
        """Angle data producer thread: periodically read servo angles
        
        Args:
            on_send: Callback function that receives angle data list
        """
        if self.robot_uids == "openarm_bi":
            num_joints = 16
            left_count = 8
            right_count = 8
        else:
            num_joints = 7

        arm_pos = [0.0] * num_joints

        period = max(1.0 / self.rate, 1e-6)
        next_time = time.monotonic()

        while not self.stop_event.is_set():
            if self.robot_uids == "openarm_bi":
                # Left arm on primary port
                for i in range(left_count):
                    response = self.send_command(self.ser_primary, f"#{i:03d}PRAD!")
                    angle = self.pwm_to_angle(response.strip())
                    if angle is not None:
                        new_angle = angle - self.zero_angles[i]
                        arm_pos[i] = np.radians(new_angle)
                    else:
                        raise ValueError(f"Left arm servo {i} response error: {response.strip()}")
                # Right arm on secondary port
                for i in range(right_count):
                    response = self.send_command(self.ser_secondary, f"#{i:03d}PRAD!")
                    angle = self.pwm_to_angle(response.strip())
                    if angle is not None:
                        new_angle = angle - self.zero_angles[left_count + i]
                        arm_pos[left_count + i] = np.radians(new_angle)
                    else:
                        raise ValueError(f"Right arm servo {i} response error: {response.strip()}")
            else:
                # Read all joint angles
                for i in range(num_joints):
                    response = self.send_command(self.ser_primary, f"#{i:03d}PRAD!")
                    angle = self.pwm_to_angle(response.strip())
                    if angle is not None:
                        # Calculate angle relative to zero position
                        new_angle = angle - self.zero_angles[i]
                        arm_pos[i] = np.radians(new_angle)
                    else: 
                        raise ValueError(f"Servo {i} response error: {response.strip()}")
            
            # Publish latest data and call callback
            self.publish_arm_pos(arm_pos)
            try:
                on_send(list(arm_pos))
            except Exception as e:
                print(f"Angle sending callback error: {e}")
                
            # Maintain fixed frequency
            next_time += period
            sleep_dt = next_time - time.monotonic()
            if sleep_dt > 0:
                time.sleep(sleep_dt)
            else:
                # If falling behind significantly, resync time
                next_time = time.monotonic()

    def pose_consumer_loop(self, on_pose):
        """Simulation control consumer thread: periodically get angle data and control simulation
        
        Args:
            on_pose: Callback function that receives action vector
        """
        period = max(1.0 / self.rate, 1e-6)
        next_time = time.monotonic()
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

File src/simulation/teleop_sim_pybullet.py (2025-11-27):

"""
Minimal PyBullet teleop for openarm_bi.

Reads 16 joint angles from two serial ports (8 per arm), subtracts calibration
offsets, maps to 18 DoF (fingers duplicated), and sends POSITION_CONTROL
commands in the PyBullet GUI.
"""

from __future__ import annotations

import argparse
import queue
import re
import time
from pathlib import Path
from typing import Dict, List

import numpy as np
import pybullet as p
import pybullet_data
import serial


def pwm_to_angle(response_str: str, pwm_min: int = 500, pwm_max: int = 2500, angle_range: float = 270):
    """Parse servo response and convert PWM to degrees."""
    match = re.search(r"P(\d{4})", response_str)
    if not match:
        return None
    pwm_val = int(match.group(1))
    pwm_span = pwm_max - pwm_min
    angle = (pwm_val - pwm_min) / pwm_span * angle_range
    return angle


def send_command(ser_obj: serial.Serial, cmd: str, sleep_s: float = 0.01) -> str:
    """Send a command to a serial device and read all available bytes."""
    ser_obj.write(cmd.encode("ascii"))
    time.sleep(sleep_s)
    response = ser_obj.read_all()
    return response.decode("ascii", errors="ignore") if response else ""


class PyBulletOpenArmBiTeleop:
    """PyBullet-based dual-arm OpenArm teleop using two serial ports."""

    JOINT_NAMES = [
        # Left arm 7
        "openarm_left_joint1",
        "openarm_left_joint2",
        "openarm_left_joint3",
        "openarm_left_joint4",
        "openarm_left_joint5",
        "openarm_left_joint6",
        "openarm_left_joint7",
        # Left fingers (2)
        "openarm_left_finger_joint1",
        "openarm_left_finger_joint2",
        # Right arm 7
        "openarm_right_joint1",
        "openarm_right_joint2",
        "openarm_right_joint3",
        "openarm_right_joint4",
        "openarm_right_joint5",
        "openarm_right_joint6",
        "openarm_right_joint7",
        # Right fingers (2)
        "openarm_right_finger_joint1",
        "openarm_right_finger_joint2",
    ]

    def __init__(
        self,
        urdf_path: Path,
        serial_left: str = "/dev/ttyUSB0",
        serial_right: str = "/dev/ttyUSB1",
        control_freq: float = 50.0,
        use_serial: bool = True,
    ):
        self.urdf_path = urdf_path
        self.control_freq = control_freq
        self.use_serial = use_serial

        # PyBullet setup
        p.connect(p.GUI)
        p.resetSimulation()
        p.setAdditionalSearchPath(pybullet_data.getDataPath())
        p.setGravity(0, 0, -9.81)
        p.loadURDF("plane.urdf")
        self.robot = p.loadURDF(
            str(self.urdf_path),
            useFixedBase=True,
            flags=p.URDF_USE_SELF_COLLISION | p.URDF_MAINTAIN_LINK_ORDER,
        )
        self.joint_name_to_idx: Dict[str, int] = {}
        for i in range(p.getNumJoints(self.robot)):
            info = p.getJointInfo(self.robot, i)
            name = info[1].decode("utf-8")
            self.joint_name_to_idx[name] = i
        missing = [n for n in self.JOINT_NAMES if n not in self.joint_name_to_idx]
        if missing:
            raise RuntimeError(f"Missing joints in URDF: {missing}")

        # Serial setup
        self.ser_left = None
        self.ser_right = None
        if use_serial:
            self.ser_left = serial.Serial(serial_left, 115200, timeout=0.01)
            self.ser_right = serial.Serial(serial_right, 115200, timeout=0.01)

        # State
        self.zero_angles = [0.0] * 16
        self.arm_pos_queue: "queue.Queue[np.ndarray]" = queue.Queue(maxsize=1)
        self.stop = False

        if use_serial:
            self._init_servos(self.ser_left, 0)
            self._init_servos(self.ser_right, 8)

    def _init_servos(self, ser_obj: serial.Serial, start_idx: int):
        """Release torque and record zero positions for one arm (8 servos)."""
        send_command(ser_obj, "#000PVER!")
        for i in range(8):
            send_command(ser_obj, "#000PCSK!")
            send_command(ser_obj, f"#{i:03d}PULK!")
            response = send_command(ser_obj, f"#{i:03d}PRAD!")
            angle = pwm_to_angle(response.strip())
            self.zero_angles[start_idx + i] = angle if angle is not None else 0.0

    def _angle_stream_loop(self):
        """Read angles from both serial ports and publish the latest 16-D array."""
        left_count = right_count = 8
        period = max(1.0 / self.control_freq, 1e-6)
        next_time = time.monotonic()

        while not self.stop:
            arm_pos_deg = [0.0] * 16
            # Left arm
            for i in range(left_count):
                response = send_command(self.ser_left, f"#{i:03d}PRAD!", sleep_s=0.008)
                angle = pwm_to_angle(response.strip())
                if angle is None:
                    continue
                arm_pos_deg[i] = angle - self.zero_angles[i]
            # Right arm
            for i in range(right_count):
                response = send_command(self.ser_right, f"#{i:03d}PRAD!", sleep_s=0.008)
                angle = pwm_to_angle(response.strip())
                if angle is None:
                    continue
                arm_pos_deg[left_count + i] = angle - self.zero_angles[left_count + i]

            arm_pos_rad = np.radians(arm_pos_deg).astype(np.float32)

            # Overwrite queue with latest
            try:
                while True:
                    self.arm_pos_queue.get_nowait()
            except queue.Empty:
                pass
            try:
                self.arm_pos_queue.put_nowait(arm_pos_rad)
            except Exception:
                pass

            next_time += period
            sleep_dt = next_time - time.monotonic()
            if sleep_dt > 0:
                time.sleep(sleep_dt)
            else:
                next_time = time.monotonic()

    @staticmethod
    def _map_to_ctrl(raw: np.ndarray) -> np.ndarray:
        """Map 16-DOF (left/right 8 joints) to 18 controls (2 gripper joints duplicated)."""
        if raw.shape[0] != 16:
            raise ValueError(f"Expected 16-length raw array, got {raw.shape[0]}")
        action = np.zeros(18, dtype=np.float32)
        # Left arm joints
        action[0:7] = raw[0:7]
        action[7] = raw[7]
        action[8] = raw[7]
        # Right arm joints
        action[9:16] = raw[8:15]
        action[16] = raw[15]
        action[17] = raw[15]
        return action

    def _set_joint_positions(self, targets: np.ndarray):
        """Send position commands to all joints."""
        for name, target in zip(self.JOINT_NAMES, targets):
            idx = self.joint_name_to_idx[name]
            p.setJointMotorControl2(
                bodyUniqueId=self.robot,
                jointIndex=idx,
                controlMode=p.POSITION_CONTROL,
                targetPosition=float(target),
                positionGain=0.2,
                velocityGain=1.0,
                force=200.0,
            )
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

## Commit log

2025-11-17 update with guideline
    [base.SLDPRT, base0.SLDPRT, config1 - base-1.STL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]
2025-11-27 update bimanual tele
    [openarm_bi.urdf]

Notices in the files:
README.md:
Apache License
